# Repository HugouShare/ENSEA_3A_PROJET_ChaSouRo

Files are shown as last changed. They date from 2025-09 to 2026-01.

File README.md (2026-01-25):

# 🤖 ChaSouRo 🤖


  

## 📝 Rapport de projet

Pour consulter notre rapport de projet [cliquez ici](Documents/Rapport%20de%20projet.md)  

---

## 👨🏽 Équipe

<div align="left">

   **🙋‍♂️ [Hugo CARVALHO FONTES](https://github.com/HugouShare)**

   **🙋‍♂️ [Nelven THÉBAULT](https://github.com/NelvTheb)**

   **🙋‍♂️ [Hugo CORDI](https://github.com/Lynxlegrand)**

   **🙋‍♂️ [Arthur Cesar NJITCHOU NKWA](https://github.com/ArthurNjitchou)**

</div>

## ⚙️ Introduction

- Nous réalisons ce projet dans le cadre de notre dernière année d'étude en spécialité électronique et systèmes embarqués à l'[ENSEA](https://www.ensea.fr/fr) située à Cergy.
- Le but du projet est de réaliser deux robots : l'un étant le robot chat et l'autre le robot souris. Les deux robots évoluent ensuite de manière autonome sur une table. Le but du jeu est alors le suivant : le robot chat doit tenter d'attraper le robot souris qui doit donc tenter d'échapper au robot chat. Une fois que le robot chat attrape le robot souris, les rôles s'inversent et la partie continue. 

## 🎯 Missions & Objectifs

Les missions principales sont les suivantes (réparties selon différents niveaux) :
  - **Niveau 0 :**
    - Le robot se déplace
    - Il ne tombe pas de la table
  - **Niveau 1 :**
    - Il détecte et se dirige vers un objet
    - Ou s’en éloigne s’il n’est pas le chat
  - **Niveau 2 :**
    - Il change de comportement (proie/prédateur) après un contact
    - Il fonctionne avec plusieurs robots sur la table
  - **Niveau 3 :**
    - Il n’est pas affecté par les obstacles hors de la table
    - Il est donc capable de se localiser

Dans notre cas à nous, nous choisissons le niveau 1 voire potentiellement, selon notre avancement, le niveau 2.  

## ⌚ Timeline du projet  

```mermaid
%%{init: {"theme":"default", "themeVariables": {
  "primaryColor": "#4F46E5",
  "primaryTextColor": "#ffffff",
  "primaryBorderColor": "#312E81",
  "lineColor": "#6366F1",
  "secondaryColor": "#E0E7FF",
  "tertiaryColor": "#A5B4FC"
}}}%%

timeline
    section Phase 1 - conception du PCB
      Séance 1 : Point réunion + schéma architectural / BOM
      Séance 2 et 3 : Schéma électronique annoté
      Séance 4 : Corrections Schéma / BOM Finale
      Séance 5 : Point réunion + placement
      Séance 6 : Placement corrigé
      Séance 7 et 8 : Routage
      Séance 9 et 10 : Corrections Routage, export...
    section Phase 2 - mécanique 3D + prise en main et programmation des différents capteurs et actionneurs
      Séance 1 : Point réunion + architecture de subsomption + architecture schéma logicielle + soudure composants sur PCBs + vérification du bon fonctionnement des PCBs
      Séance 2 et 3 et 4 : Prise en main & programmation du LiDar + accéléromètre + écran OLED + module bluetooth avec développement application apk
      Séance 5 : Point réunion + vérification du bon fonctionnement des différents modules
      Séance 6 et 7 et 8 : Développement de l'odométrie + programmation des moteurs + 1x TOF puis 4x TOFs + modification de la structure mécanique du robot pour intégration des 4 TOFs et écran OLED
      Séance 9 et 10 : Impression 3D de la structure mécanique du robot + début de l'intégration des différents modules + finalisation de la programmation des 4x TOFs ensemble 
    section Phase 3 - Intégration, tests & vérifications
      Séance 1 et 2 : Point réunion + intégration, tests & vérifications
      Séance 3 : DEMONSTRATION FINALE
```

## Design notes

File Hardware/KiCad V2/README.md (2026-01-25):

# Modifications sur la V1

- Problèmes sur la taille des empreintes pour les capacités >= 10uF -> Passage en 0603
- Changement pad sw wurth vers un connecteur (plus propre) -> JST_PH Batterie +/- (Pin_x2) en JS_PH_ Batterie +/- et +/IN du switch wurth (Pin_x4)
- Erreur sur un des deux drivers où les silkscreen des OUT1 et OUT2 sont inversé par rapport au pin (Quand on se place dans le sens avec TX4/RX4 du ST-Link -> Driver gauche)
- Ajout Silkscreen sur ST-Link pour simplifier la connexion
- Modification schématique/Nom du bon NMOSFET -> SQ2310ES
- Changement de la capacité de découplage du VDDA : 47uF -> 22uF
- Oublie des capacités pour limiter les rebonds sur USER1 et USER2 -> ajout de 0.1uF
- Inversion sur le PCB des RX3/TX3 sur les pins PB10/PB11 du STM32
- Problème d'angle droit sur la ligne SDA3 enlevé (peut-être incidence sur l'I2C3)
---
Modification non faite mais à connaître pour de futurs projets 
- Utilisation du PB4 (BOOT0) pour le xshunt du ToF1 → pose problème car relié en interne à un GPIO relié ici au FWD ou REV d'un driver moteur → réinitialise la carte.
    - Solution : ne jamais utiliser la broche `BOOT0` pour autre chose même si l'on est censé pouvoir le faire

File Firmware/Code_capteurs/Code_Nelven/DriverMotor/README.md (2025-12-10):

# Fonctionnement

## Init 

- Fonction `Init_motors()` qui démarre les PWM et fais tourner le robot sur lui même à gauche puis à droite.

## Principe
- Une structure de pointeurs motorDriver à été mis en place qui associe à un moteur L ou R, son timer et son FWD/REV.
- 2 fonctions
	- `Motors_Set()` qui vient modifier une structure avec les valeurs de vitesses et durées souhaitées dans les deux moteurs
	- `Motor_SetSpeed()` qui applique dans la tâche `Task_motor` dédiée et permet au tout de ne pas être bloquant 

## Utilisation

Ici configuré dans le callback des boutons 2 consignes :  
- une où le robot tourne sur lui même sens droite
- une où le robot avance tout droit lentement

Reste à mettre en plac ue fonction pour corrige la trajectoire qui n'est pas parfaitement droite.

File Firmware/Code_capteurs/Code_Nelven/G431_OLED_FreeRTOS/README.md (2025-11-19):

# ATTENTION

Drivers dans ../Drivers à ajouter dans le path pour que ça marche

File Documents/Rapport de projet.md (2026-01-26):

# Sommaire  

<details>
<summary><strong>📑 Sommaire</strong> (cliquer pour dérouler)</summary>

<br>

- [Contexte général du projet](#contexte-général-du-projet)
- [Aspects techniques liés au projet](#aspects-techniques-liés-au-projet)
  - [Schéma d'architecture fonctionnelle](#schéma-darchitecture-fonctionnelle)
  - [Diagramme des tâches](#diagramme-des-tâches)
  - [Organisation du projet sur STM32CubeIDE](#organisation-du-projet-sur-stm32cubeide)
    - [Description détaillée fichiers sources](#-description-détaillée-fichiers-sources)
    - [Description détaillée fichiers headers](#-description-détaillée-fichiers-headers)
- [Point HARDWARE](#point-hardware)
  - [Composants](#composants)
  - [Schéma électrique](#schéma-électrique)
  - [Routage](#routage)
    - [Positionnement face F/B](#positionnement-face-fb)
    - [Positionnement sur la carte](#positionnement-sur-la-carte)
- [Point FIRMWARE](#point-firmware)
  - [Choix d’architecture logicielle](#choix-darchitecture-logicielle)
  - [Choix de FreeRTOS](#choix-de-freertos)
  - [Gestion de la mémoire](#gestion-de-la-mémoire)
  - [Choix et description des comportements du robot](#choix-et-description-des-comportements-du-robot)
- [Problèmes rencontrés lors du projet](#problèmes-rencontrés-lors-du-projet)
  - [Hardware](#hardware)
  - [Firmware](#firmware)
- [Rapport individuel des tâches réalisées](#rapport-individuel-des-tâches-réalisées-au-sein-du-projet)
- [Résultat final le jour J](#résultat-final-le-jour-j)
- [Conclusion du projet](#conclusion-du-projet)

</details>  

# Contexte général du projet  

Comme expliqué précédemment, le but de notre projet est de concevoir un robot capable de jouer au jeu du chat et de la souris de manière complètement autonome sur une table.   
Pour plus d'informations sur le projet : [cliquez ici](Descriptif%20du%20projet.pdf)  

Pour se faire, seuls les composants utilisés dans le projet nous sont imposés : [liste des composants](Liste%20des%20composants%20disponibles.pdf)  

Charge à nous :  
- de développer une PCB
- de programmer les différents modules : capteurs, actionneurs, écran OLED et module de communication bluetooth
- d'intégrer tous les modules ensemble, de tester et vérifier le bon fonctionnement de l'ensemble

# Aspects techniques liés au projet

## Schéma d'architecture fonctionnelle  

Après une première réunion portant sur l'architecture fonctionnelle de notre robot, voici le schéma fonctionnel que nous adoptons pour notre robot :  
  

## Diagramme des tâches  

Voici un diagramme des tâches qui résume le fonctionnement de notre robot :

  

Les priorités étant définies dans le fichier de configuration `freeRTOS_tasks_prority.h` :

```c
#define ADXL_TaskRead_PRIORITY 2
#define ADXL_TaskPrint_PRIORITY 1

#define task_ROOMBA_PRIORITY 6
#define task_CHAT_PRIORITY 2
#define task_SOURIS_PRIORITY 2
#define task_EDGE_PRIORITY 6

#define task_Control_PRIORITY 5

#define task_ENC_D_Update_PRIORITY 6
#define task_ENC_G_Update_PRIORITY 6
#define task_Odom_Update_PRIORITY 3

#define task_BLUETOOTH_TX 1
#define task_BLUETOOTH_RX 2

#define task_LIDAR_Update_PRIORITY 3

#define task_motor_PRIORITY 5

#define task_screen_PRIORITY 1
```

## Organisation du projet sur STM32CubeIDE  

D'un point de vue global, nous avons choisi d'organiser notre projet de la manière suivante :  

| Fichiers sources | Fichiers headers |
|---|---|
|  |  |  

### 📝 Description détaillée fichiers sources

#### 📦 Dossier `actuators/` – Gestion des actionneurs

| Fichier | Rôle |
|---|---|
| **behavior.c** | Implémente les comportements de haut niveau (navigation et stratégie de déplacement). |
| **control.c** | Contient les fonctions de contrôle moteur, coordination PID, gestion des vitesses/couple. |
| **encoder.c** | Gestion des encodeurs : lecture des ticks, calcul de vitesse et position. |
| **motor.c** | Interface bas niveau pour piloter les moteurs (PWM, direction, enable/disable). |
| **pid.c** | Implémentation des régulateurs PID utilisés par `control.c` et `behavior.c`. |

#### 📦 Dossier `bluetooth/` – Communication Bluetooth

| Fichier | Rôle |
|---|---|
| **bluetooth.c** | Gestion du module Bluetooth : initialisation, envoi/réception de données. |

#### 📦 Dossier `oled_screen/` – Afficheur OLED

| Fichier | Rôle |
|---|---|
| **oled.c** | Gestion d’un écran OLED : affichage de texte, images, et initialisation. |

> Remarque : Drivers OLED importé depuis internet et modifié se situant dans le dosser `Drivers/OLED/`.

#### 📦 Dossier `sensors/` – Capteurs du robot

| Fichier | Rôle |
|---|---|
| **accelerometers.c** | Lecture de l’accéléromètre (IMU), calibration, filtrage. |
| **lidar.c** | Interface avec un LiDAR : récupération des distances, gestion du capteur. |
| **tofs.c** | Gestion des capteurs Time-of-Flight. |

#### 🧵 FreeRTOS

| Fichier | Rôle |
|---|---|
| **app_freertos.c** | Définition des tâches FreeRTOS, files de messages, mutex et scheduling. |

#### ⚙️ Core système

| Fichier | Rôle |
|---|---|
| **main.c** | Point d’entrée du programme, initialisations des différents capteurs, créations des différentes tâches et démarrage du RTOS. |
| **syscalls.c** | Implémente les fonctions système nécessaires (malloc, printf…). |
| **sysem.c** | Gestion du système et interrupt handlers (auto-généré). |
| **system_stm32g4xx.c** | Configuration de l’horloge système et initialisation MCU. |

#### 🔧 Drivers Hardware Abstraction Layer (HAL)

| Fichier | Rôle |
|---|---|
| **dma.c** | Initialisation du DMA pour les transferts mémoire ↔ périphériques. |
| **gpio.c** | Configuration des broches GPIO (mode, pull-up/down, vitesse…). |
| **i2c.c** | Initialisation du bus I2C utilisé par IMU, OLED, ToF. |
| **tim.c** | Configuration des timers : PWM moteurs, interruptions, timebase. |
| **usart.c** | Gestion de la communication série UART (console, Bluetooth). |
| **stm32g4xx_hal_msp.c** | Fonctions MSP auto-générées : clocks, GPIO, interruptions. |
| **stm32g4xx_it.c** | Gestion des interruptions globales du microcontrôleur. |
| **stm32g4xx_hal_timebase_tim.c** | Gestion de la base de temps HAL via TIM. |  

### 📝 Description détaillée fichiers headers

#### 📦 Dossier `oled_screen/` – Gestion de l’OLED

| Fichier | Rôle |
|---|---|
| **bitmaps.h** | Ressources graphiques (icônes, images) utilisées par l’écran OLED. |  

#### 🧵 FreeRTOS

| Fichier | Rôle |
|---|---|
| **FreeRTOSConfig.h** | Configuration du kernel FreeRTOS (priorités, timers, heap…). |
| **freeRTOS_tasks_priority.h** | Définition des priorités de tâche et organisation du multitâche. |

#### ⚙️ Core du programme

| Fichier | Rôle |
|---|---|
| **main.h** | Déclarations globales, includes principaux et prototypes de `main.c`. |

# Point HARDWARE  

> Remarque :  
> Pour évaluer la partie hardware, merci de vous référer au KiCAD V2, étant donné que les problèmes identifiés ont été corrigés et le schéma refait au propre. La V1 n’a pas été modifiée afin de rester la plus fidèle possible à la version physique reçue et utilisée.

### Composants

Nous avions pour les missions principales, une liste de composants que nous devions utiliser ce qui a conditionné nos choix mais les a aussi simplifiés.
Voici les composants ajoutés :
- Écran OLED → ssd1306 
  - écran personnel de Nelven pour pouvoir le comprendre et le réutiliser pour de prochains projets.
- Bipper
  - Ajout d'un bipper pour avoir un différent moyen des autres groupes de notifier des choses (mode chat par exemple).
- Connecteurs JST-PH
  - Un pas de 2.0mm permettant de mettre tous les connecteurs sur une face du PCB ce que ne permettait pas les JST-XH (2.54mm) et en étant plus simple à souder/connecter que des JST-SH(1.0mm).

### Schéma électrique

Dans cette partie il n'y a pas grand chose à ajouter, étant donné que les circuits on été réalisé à l'aide des datasheet, de mes propres connaissances sur d'anciens projets.

### Routage

#### Positionnement face F/B

Un choix a été effectué afin de simplifier la soudure :

- Tous les composants passifs, régulateurs et transistors sont placés sur une même face du PCB.
- Tous les connecteurs, SoC, quartz, condensateurs électrolytiques, LED et boutons sont placés sur l’autre face.

De cette manière, sur la face inférieure, il est possible d’observer les circuits et de souder l’ensemble des petits composants au four en une seule opération.
Sur la face supérieure (visible) se trouvent les SoC, les connecteurs et les LED, c’est-à-dire les unités et modules nécessaires au fonctionnement du système, ainsi que les composants les plus volumineux à souder.

#### Positionnement sur la carte

J'ai choisi de ne pas mélanger les parties puissance et signal à différents endroits de la carte. En considérant que le bas du PCB se trouve au niveau du branchement de la batterie, j'ai positionné les composants de la manière suivante :

- **Bas du PCB → partie puissance**
  - Arrivée de la batterie [bas gauche]  
  - Interrupteur d’alimentation ON/OFF [bas gauche]  
  - Convertisseurs $V_{BATT}/5V$ et $5V/3.3V$ [bas milieu]  
  - Condensateur électrolytique [bas milieu]  
  - Drivers moteurs (alimentés en $V_{BATT}$)  
    - Carte retournée sur le robot : driver droit à [bas gauche] et driver gauche à [bas droit], pour simplifier les branchements  

- **Milieu/Haut du PCB → partie signal**
  - MCU [milieu]  
  - Connecteur ST-Link [haut droit]  
  - ADXL [haut droit]  
  - Quartz [milieu] avec ses deux condensateurs de l’ordre de la dizaine de nanofarads  
  - Boutons [haut gauche]  
  - 3 LED [haut gauche]  
    - **ROUGE** : $3.3V$, allumée en permanence lorsque la carte est sous tension  
    - **BLEU** : LED1 pour programmation/debug  
    - **VERT** : LED2 pour programmation/debug

À noter que j'ai respecté les consignes de routage pour le `convertisseur buck` fournies dans la datasheet, ce qui occupe une certaine place sur la carte.

Et tout autour de la carte les différents connecteurs pour tout relié à la carte.

`Face avant` :

Face avant PCB  

`Face arrière` :

Face arrière PCB  

# Point FIRMWARE  

La partie firmware du projet a été conçue afin de garantir un fonctionnement **modulaire, robuste et évolutif** du robot, tout en respectant les contraintes d’un système embarqué temps réel (ressources mémoire limitées, concurrence des tâches et réactivité élevée).

### Choix d’architecture logicielle  

#### Organisation du code et séparation des modules  

Le code C a été structuré par **fonctionnalité**, chaque module correspondant à un sous-système clairement identifié du robot (capteurs, actionneurs, communication, affichage, comportements). Cette organisation permet :
- une **lisibilité accrue** du code,
- une **maintenance facilitée**,
- une **intégration progressive** et maîtrisée des différents modules.

Chaque dossier (par exemple `sensors/`, `actuators/`, `bluetooth/`, `oled_screen/`) contient les fichiers sources associés à un module donné, incluant les structures de données, les fonctions de configuration et la logique de traitement.

#### Convention d’intégration des modules (init, tâches et callbacks)  

Afin de faciliter l’intégration et d’assurer une architecture cohérente sur l’ensemble du projet, une **convention commune** a été adoptée pour tous les drivers.

Pour chaque module :
- une fonction **`XXX_init()`** est définie afin d’initialiser le périphérique (configuration matérielle, paramètres internes, états initiaux),
- une fonction **`XXX_task_create()`** est fournie pour créer la ou les tâches FreeRTOS associées au module.

Ces deux fonctions sont **appelées explicitement dans `main.c`**, ce qui permet :
- de centraliser l’initialisation du système,
- de maîtriser précisément l’ordre de démarrage des modules,
- de simplifier l’ajout ou le retrait d’un module sans impacter les autres parties du code.

Lorsque l’utilisation de **callbacks** est nécessaire (interruptions, réception UART, DMA, timers…), ceux-ci sont **redéfinis uniquement dans `main.c`**. Les callbacks HAL appellent ensuite des fonctions dédiées du type **`XXX_callback()`** appartenant au module concerné.

Cette approche permet :
- d’éviter toute **double redéfinition de callbacks**, source potentielle de conflits,
- de conserver une **séparation claire** entre la couche HAL et la logique applicative,
- d’améliorer la lisibilité et la maintenabilité du code.

#### Utilisation de drivers dédiés  

Le choix de développer des **drivers spécifiques** pour chaque périphérique (LIDAR, TOF, ADXL, moteurs, encodeurs, Bluetooth…) permet d’abstraire les accès bas niveau (I2C, UART, GPIO, timers) et de proposer une interface logicielle homogène.

Les drivers s’appuient sur la HAL STM32 pour les accès matériels, tout en encapsulant la logique propre à chaque capteur ou actionneur. Cette approche améliore :
- la **réutilisabilité** du code,
- la **robustesse de l’intégration**,
- la facilité de test et de débogage.

### Choix de FreeRTOS  

L’utilisation de **FreeRTOS** s’est imposée au vu de la complexité du système et du nombre de traitements à effectuer en parallèle : lecture capteurs, contrôle moteur, communication Bluetooth et prise de décision.

Chaque fonctionnalité critique du robot est implémentée sous forme de **tâche FreeRTOS dédiée**, permettant :
- une **exécution concurrente maîtrisée**,
- une **priorisation fine** des traitements,
- une meilleure **réactivité temps réel**.

Les **priorités des tâches FreeRTOS sont toutes définies dans un header dédié** (`freeRTOS_tasks_priority.h`), ce qui permet :
- une vision globale et centralisée de l’ordonnancement,
- une modification simple des priorités sans impacter le reste du code,
- une meilleure cohérence entre les différents modules.

La synchronisation entre tâches est assurée via les mécanismes FreeRTOS classiques (sémaphores, mutex, notifications), garantissant la cohérence des données partagées.

### Gestion de la mémoire  

Les contraintes mémoire, en particulier sur la RAM, ont fortement influencé les choix firmware. L’utilisation de FreeRTOS et de certains modules gourmands (LIDAR, OLED) a conduit à :
- une gestion stricte des piles de tâches,
- une limitation des buffers statiques,
- le retrait de l’écran OLED dans la version finale afin d’éviter tout stack overflow.

Le tas FreeRTOS a été dimensionné à sa valeur maximale acceptable (~25 kB) pour garantir la stabilité du système.

### Choix et description des comportements du robot  

Le comportement global du robot repose sur une **machine à états finis** comportant quatre modes principaux : ROOMBA, CHAT, SOURIS et EDGE. Chaque mode correspond à un objectif précis et exploite les données issues des capteurs.

#### Mode ROOMBA  

Le mode ROOMBA correspond à un comportement d’exploration autonome :
- déplacement continu,
- évitement des bords via les capteurs TOF et le LIDAR,
- changements de direction pseudo-aléatoires.

Il constitue le **mode par défaut** lorsque aucune cible n’est détectée.

#### Mode CHAT  

Le mode CHAT est activé lorsqu’une cible est détectée :
- traitement des données LIDAR (tri, clustering, sélection de la cible),
- poursuite active de l’adversaire,
- ajustement dynamique de la trajectoire par asservissement moteur.

#### Mode SOURIS  

Le mode SOURIS correspond à un comportement de fuite :
- activation lorsque le robot est détecté ou poursuivi,
- recherche d’un espace libre,
- déplacements rapides tout en évitant les bords.

#### Mode EDGE  

Le mode EDGE est un mode de sécurité prioritaire :
- déclenché dès qu’un bord est détecté,
- arrêt ou recul immédiat du robot,
- réorientation avant reprise d’un autre mode.

Ce mode est volontairement prioritaire afin de garantir la sécurité du robot, indépendamment du comportement en cours.

### Coordination des comportements  

Les transitions entre les différents modes sont déclenchées par les données capteurs, le contexte global du robot et les événements temps réel. Cette organisation permet d’obtenir un comportement **autonome, cohérent et réactif**, tout en restant facilement extensible.

# Problèmes rencontrés lors du projet    

### Hardware

Du côté Hardware, les problèmes rencontrés ont été solutionnés dans la V2 que l'on trouve dans `Hardware/KiCad V2/` avec readme associé qui explique les changement :

> Remarque : la carte physique utilisée reste la V1 ; cette V2 constituerait donc sa remplaçante dans le cas où l’on souhaiterait améliorer le projet.

#### Modifications sur la V1

- Problèmes sur la taille des empreintes pour les capacités >= 10uF -> Passage en 0603
- Changement pad sw wurth vers un connecteur (plus propre) -> JST_PH Batterie +/- (Pin_x2) en JS_PH_ Batterie +/- et +/IN du switch wurth (Pin_x4)
- Erreur sur un des deux drivers où les silkscreen des OUT1 et OUT2 sont inversé par rapport au pin (Quand on se place dans le sens avec TX4/RX4 du ST-Link -> Driver gauche)
- Ajout Silkscreen sur ST-Link pour simplifier la connexion
- Modification schématique/Nom du bon NMOSFET -> SQ2310ES
- Changement de la capacité de découplage du VDDA : 47uF -> 22uF
- Oublie des capacités pour limiter les rebonds sur USER1 et USER2 -> ajout de 0.1uF
- Inversion sur le PCB des RX3/TX3 sur les pins PB10/PB11 du STM32
- Problème d'angle droit sur la ligne SDA3 enlevé (peut-être incidence sur l'I2C3)
---
> [!IMPORTANT]
> Modification non faite mais à connaître pour de futurs projets 
> - Utilisation du PB4 (BOOT0) pour le xshunt du ToF1 → pose problème car relié en interne à un GPIO relié ici au FWD ou REV d'un driver moteur → réinitialise la carte.
>    - Solution : ne jamais utiliser la broche `BOOT0` pour autre chose même si l'on est censé pouvoir le faire

#### PIN BOOT0

Même si cela constitue une répétition par rapport aux lignes précédentes, nous tenons à insister sur le fait que, sur les STM32, bien qu’il soit parfois possible d’utiliser la broche `BOOT0` selon le microcontrôleur, il est fortement déconseillé de le faire. En effet, cela peut entraîner des problèmes de fonctionnement, comme observé avec les capteurs ToF ci-dessus, mais également compliquer la programmation.

Dans notre cas, nous avons dû utiliser `STM32CubeProgrammer` afin de configurer par logiciel la mémoire de démarrage (boot memory). Ainsi, au redémarrage, la carte démarrait correctement sur le programme flashé, alors qu’auparavant il était nécessaire de laisser la carte constamment sous tension si l’on voulait éviter de devoir reprogrammer le code avec un ST-Link.

### Firmware

Du côté firmware, l’un des premiers problèmes que nous avons dû résoudre est la gestion de la mémoire, et plus particulièrement de la RAM (~91 %), étant donné que notre ROM n’a atteint que ~41 %. Nous avons donc fait le choix de retirer l’écran OLED dans la version finale afin d’éviter tout stack overflow et de monter le tas FreeRTOS à sa valeur maximale avant overflow (25 000 octets, soit environ 25 kB).

Deux autres problèmes majeurs ont été rencontrés durant le projet. D’une part, le LIDAR présentait des angles morts, ce qui a nécessité une adaptation de la stratégie de gestion des trames envoyées par le capteur, ainsi qu’un ajustement de la fréquence de traitement du buffer stockant les données issues de ces trames, afin d’améliorer la couverture et la fiabilité de la détection. D’autre part, le réglage des correcteurs PID s’est avéré particulièrement délicat, demandant de nombreuses itérations et de longues phases de tests expérimentaux pour obtenir un comportement stable et satisfaisant du robot.

# Rapport individuel des tâches réalisées au sein du projet  

Suite à cela, après une nouvelle réunion, chaque membre du groupe se voit attribuer diverses missions.  
Voici un récapitulatif de ce que chaque membre du groupe aura réalisé au sein du projet...  

### Nelven THEBAULT  

`Hardware` :
- PCB
  - Conception du PCB finalement retenu
  - Schéma électrique
  - Routage
  - Soudure
  > J’explique mes choix par rapport au cahier des charges et à nos réunions de projet avec l’équipe dans la partie [Point HARDWARE](#point-hardware).

`Firmware` :
- Module Moteur
  - Conception du **driver moteur** et **task_motor**
  - Conception du code **encodeur (ENC)** ensuite repris par Hugo  pour FreeRTOS
- Module OLED 
  - Conception du **oled.c** et **task_oled** utilisant un driver générique
- Module Bipper
  - Intégration du **Bipper** dans certaines parties du code (mode chat par exemple)
- Intégration des différents modules 

`Mécanique` :
- Participation aux choix pour la conception mécanique avec Arthur
- Impressions 3D de certaines parties
- Assemblage de certaines parties

### Hugo CARVALHO FONTES  

`Hardware` : 
- Conception d'une PCB : schematique & routage
- Soudure des composants sur la carte finale
- Analyses oscilloscope & modification du pin XSHUT1 car disfonctionnnement  

`Software` : 
- Module bluetooth HC-05
  - Création d'une application apk sous android studio afin de pouvoir lancer le robot ou l'arrêter d'urgence, mais aussi afin de recevoir et afficher en temps-réel les coordonnés du robot sur la table

`Firmware` : 
- Module bluetooth HC-05
  - Implémentation du code C en Free-RTOS et avec driver sur STM32G431CBU6
- Module TOFs VL53L0X
  - Implémentation du code C en Free-RTOS et avec driver sur STM32G431CBU6 afin de faire fonctionner 4 TOFs ensemble
- Module accéléromètre ADXL345
  - Implémentation du code C en Free-RTOS et avec driver sur STM32G431CBU6
- Intégration & vérification de tous les différents modules afin d'obtenir un robot fonctionnel  

### Arthur César NKWA NJITCHOU  

`Hardware` :
- Conception d'un PCB : Réalisation de la schématique et du routage du circuit imprimé (PCB)
- Recherche de composants : Participation active à la sélection des composants électroniques
- Soudure : Assemblage et soudure des composants sur le PCB final avec l'équipe

`Software` :
- Développement en C : Implementation du code pour l'accéléromètre ADXL345, permettant de détecter les chocs brusques lors des collisions du robot

`Mécanique` :
- Conception des supports : Création de supports pour les capteurs TOF et l'écran, ainsi que perçage pour l'interrupteur et le buzzer
- Amélioration des pattes : Optimisation des pattes des bases supérieures pour une meilleure stabilité
- Impression 3D : Impression des différentes parties du robot à l'aide d'une imprimante 3D
- Assemblage partie mécanique du robot.

### Hugo CORDI  

`Software/Firmware` :
- Module LIDAR
  - Développement du traitement des données LIDAR pour la détection des ennemis
  - Implémentation d’algorithmes de clustering, tri et sélection de la cible
  - Exploitation des données pour alimenter les décisions de poursuite et de fuite du robot
  - Implémentation en C embarqué sous FreeRTOS sur STM32, avec gestion des tâches, de la mémoire et synchronisation via sémaphores, notifications et mutex
  - Intégration du module LIDAR avec les autres capteurs et les comportements globaux du robot

- Module encodeurs roues
  - Gestion des encodeurs incrémentaux pour l’estimation du déplacement du robot
  - Implémentation d’un asservissement en position à l’aide de correcteurs PID
  - Réglage et validation des performances de déplacement
  - Implémentation en C embarqué sous FreeRTOS sur STM32, avec communication et synchronisation avec les autres modules du système
  - Contribution à l’intégration globale du robot afin d’obtenir un système autonome et fonctionnel

- Code de comportement du robot
  - Conception et implémentation d’une machine à états à quatre modes (ROOMBA, Chat, Souris, Edge)
  - Gestion des transitions d’états en fonction des données capteurs et du contexte
  - Implémentation en C embarqué sous FreeRTOS, avec coordination des tâches et synchronisation entre modules pour assurer un comportement autonome et réactif  

# Résultat final le jour J  

`Robot`:

Robot  

`Test détection de bord en mode ROOMBA` :

https://github.com/user-attachments/assets/2c88ca6d-3d82-48a8-8c14-df83039007b4

cf. chemin : <Images et videos pour rapport de projet/Test detection de bord mode ROOMBA.mp4>  

`Test plusieurs robots qui sont chats` :  

https://github.com/user-attachments/assets/9dab9074-2687-4d48-a438-ce1f9aacd102

cf. chemin : <Images et videos pour rapport de projet/Test plusieurs chats.mp4>  

# Conclusion du projet   

Le projet a permis de concevoir un robot autonome capable de jouer au jeu du chat et de la souris, en intégrant de manière cohérente la partie hardware, firmware et mécanique. Nous avons pu appliquer nos connaissances en conception de PCB, programmation C et utilisation de FreeRTOS, tout en respectant les contraintes des composants imposés.

Les différentes étapes, de la conception des schémas et du routage à l’implémentation des modules moteurs, capteurs et communication, ont permis de créer un robot fonctionnel et robuste. Ce projet nous a également confrontés à des problématiques concrètes, telles que la gestion de la mémoire, les choix de routage pour éviter les interférences et la configuration des broches critiques comme BOOT0. Il a renforcé notre capacité à travailler en équipe, à coordonner les tâches entre hardware, firmware et mécanique, et à documenter nos choix pour faciliter la maintenance et l’évolution future du robot.

Enfin, nous sommes fiers d’avoir atteint notre objectif : le robot détecte les bords et peut jouer au chat et à la souris, malgré certaines limitations comme l’écran, la vitesse, l'ajout de la tâche qui permet le  changement de rôle lors d'un choc, du déplacement à optimiser et la détection à calibrer plus finement. Ce succès constitue une expérience complète et enrichissante dans le domaine des systèmes embarqués.

<p float="left">

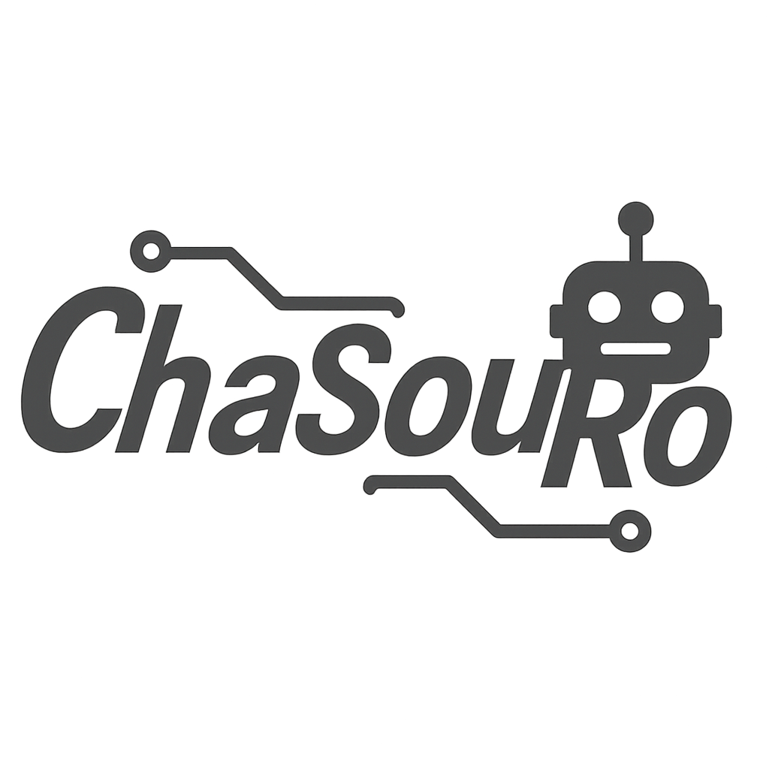
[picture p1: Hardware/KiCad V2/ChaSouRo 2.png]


</p>

`Photo de l'équipe ChaSouRo` :

Equipe projet

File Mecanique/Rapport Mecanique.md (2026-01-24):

# Partie Mécanique du Projet Chat et Souris

Nous nous sommes inspirés de la version de base fournie par le professeur [ici](https://cad.onshape.com/documents/7eabf90e47e8c8553dc09658/w/3dcd7f2858a0589a4cbae030/e/145e161f6c9d99158433c942).

## Modifications et Améliorations

### Conception des Supports
- **Supports TOF** : Création de supports robustes pour les capteurs TOF, optimisant l'alignement pour une détection précise des obstacles.



- **Support de l'Écran** : Développement d'un support ergonomique pour l'écran, garantissant une visualisation claire tout en préservant la compacité du robot.



### Perçage et Assemblage
- **Perçage** : Réalisation de trous pour intégrer l'interrupteur et le buzzer, assurant une installation harmonieuse des composants électroniques.
- **Optimisation des Pattes** : Amélioration des pattes de la base supérieure pour renforcer la stabilité et l'équilibre du robot lors de ses déplacements. Nous avons effectué des tests pour obtenir les dimensions exactes, garantissant ainsi que chaque composant s'encastre facilement et puisse être retiré sans résistance excessive.

WhatsApp Image 2026-01-24 at 09 39 03

**Base supérieure : 1. trous buzzer, 2. trous interrupteur 3. Pattes**

### Impression 3D
- **Fabrication** : Impression 3D de diverses pièces du robot, permettant un ajustement précis au design global et facilitant la personnalisation des composants.

## Assemblage
Assemblage de tous les composants afin de permettre les tests logiciels.



**Assemblage final**

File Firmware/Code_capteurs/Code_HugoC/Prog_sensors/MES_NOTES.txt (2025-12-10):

##### CONFIGURATION #####
0-Mettre les inits dans le main.c et les includes dans main.h
1-Ouvrir STM32CubeProgrammer et configurer les Option Bytes du microcontroller (Voir dossier concerné)
2-Remplacer dans les headers "stm32l4xx_hal.h" par "stm32g4xx_hal.h"
3-Dans l'ioc, activer le DMA pour l'usart approprié
4-Dans l'ioc, activer PWM generation pour le gpio de controle de la vitesse du LIDAR
5-Dans l'ioc, activer les Hooks (pour les stack overflow et les malloc) et highwatermark pour l'espace mémoire
6-Flash le code de la carte

##### MES NOTES #####

- finir le code de détection des ennemis
- régler les encodeurs
- faire les task et la machine à états
- faire le code de l'odométrie
- tout mettre sous RTOS
- intégrer le code dans le vrai capteur

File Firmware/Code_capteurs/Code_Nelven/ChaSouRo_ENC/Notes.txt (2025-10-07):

Explications :
- Encodeur -> TIM4 encoder mode (CH1&CH2) en mode TI1&TI2
- Timer périodique pour lire -> TIM2 (ici à 5 Hz)
- Affichage UART2 à la période de TIM2 de Position 
et vitesse ang avec le nb de tour avant/arrières
grâce à FWD/REV.
- LED2 de la nucleo est toggled dès que le moteur tourne

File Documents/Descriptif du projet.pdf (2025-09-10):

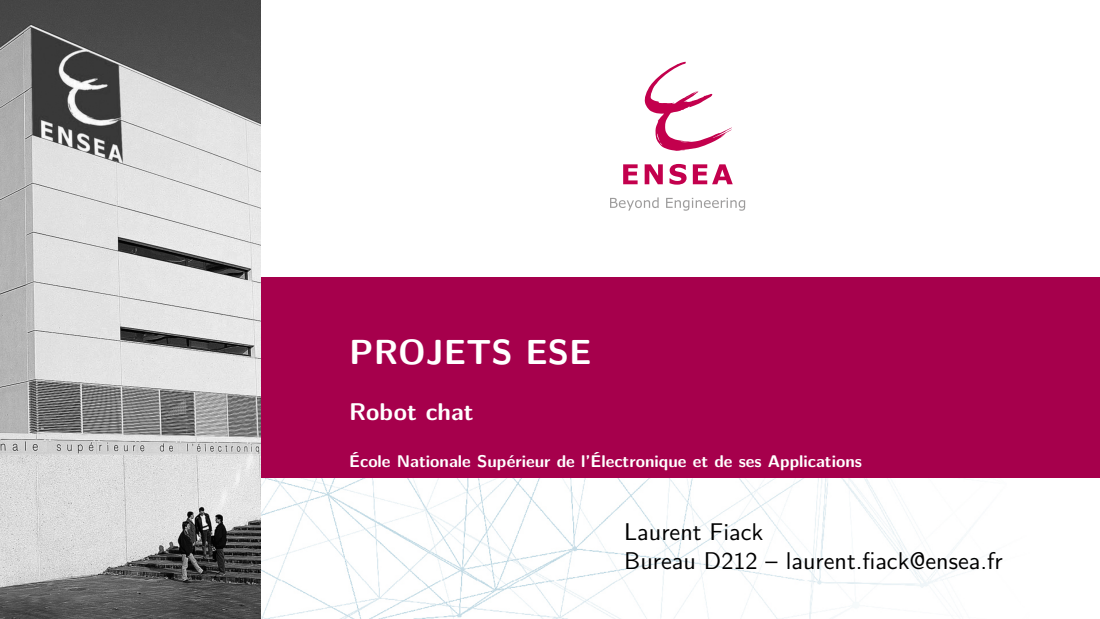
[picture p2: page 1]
PROJETS ESE; Robot chat

École Nationale Supérieur de l’Électronique et de ses Applications

Laurent Fiack
Bureau D212 – laurent.fiack@ensea.fr

Objectifs

## Objectifs

Concevoir un système embarqué de A à Z (du PCB jusqu’au Firmware) Électronique, microcontrôleur, capteurs (conditionnement), actionneurs (drivers), HMI Firmware, drivers, temps-réel
Code de haut niveau, stratégie, comportement...
Projet réparti sur plusieurs modules
Système à Microcontrôleurs → PCB
Noyaux temps-réel → Écriture des drivers logiciels
Initiation à la robotique → Comportement/Stratégie
Projets prétexte pour étudier différents aspects des systèmes embarqués Concevoir un robot mobile qui joue à "chat" avec d’autres robots.
L. Fiack 2 / 10

Projet challenge robot-chat

## Projet challenge robot-chat

Plusieurs robots évoluent sur une table
La table n’a pas de bordure : les robots peuvent tomber Un robot est le "chat"
Il doit attraper un autre robot
Le robot attrapé devient le nouveau "chat"
Et ainsi de suite
L. Fiack 3 / 10

Projet challenge robot-chat

## Sous-objectifs : Robot chat

Projet modulaire.
Objectif simple pour inclure tout le monde. Niveau 0 :
Le robot se déplace,
Il ne tombe pas de la table.
Niveau 1 :
Il détecte et se dirige vers un objet,
Ou s’en éloigne s’il n’est pas le chat.
Niveau 2 :
Il change de comportement (proie/prédateur) après un contact, Il fonctionne avec plusieurs robots sur la table.
Niveau 3 :
Il n’est pas affecté par les obstacles hors de la table,
Il est donc capable de se localiser.
L. Fiack 4 / 10

Projet challenge robot-chat

## Challenge et sous-objectifs

Soyez clair sur vos objectifs !
Pour aller plus loin : Objectifs secondaires, quêtes annexes et challenges Recharge de batterie (avec un câble)
Station de recharge
Robot qui consomme le moins
Robot qui coûte le moins cher
Robot le plus rapide
Fusion de données (IMU, odométrie...) ...
L. Fiack 5 / 10

Déroulement

## Déroulement

Jusqu’à la toussaint
Électronique et mécanique
TP de Microcontrôleurs
Vacances toussaint : Samedi 25 octobre au Dimanche 2 novembre Entre la toussaint et noel
Bibliothèques logicielles
Drivers
Organisation du code
TP de Noyaux temps-réel
Stratégie et comportements
TP d’Introduction à la robotique
Vacances noel : Samedi 20 décembre au Dimanche 4 janvier Après noel
Dernière séance : stratégie et comportements
TP d’Introduction à la robotique
Challenge le vendredi 16 janvier
Fin du semestre : Samedi 17 janvier
Début des PFE : Lundi 19 janvier
L. Fiack 6 / 10

## Attention

Découper le projet
Faire un planning !
Deux semaines de délai (ou plus !) pour les commandes Prendre en compte le temps de soudure, assemblage, tests Commandes au plus tard mi-octobre (ça arrive vite !)
L. Fiack 7 / 10

## Deadlines

10 séances de Systèmes à microprocesseurs
1 | Séance 1 : Schéma architectural / BOM
2 | Séance 2 et 3 : Schéma électronique annoté
3 | Séance 4 : Corrections Schéma / BOM Finale
4 | Séance 5 : Placement
5 | Séance 6 : Placement corrigé
6 | Séance 7 et 8 : Routage
7 | Séance 9 et 10 : Corrections Routage, export...
+ 4h de TD dédié
L. Fiack 8 / 10

## Évaluation

Systèmes à microcontrôleurs : Évaluation des rendus + 1 rapport technique À la toussaint
4 crédits sur 5 dans le module
Noyau temps-réel : Revue de code (git) + 1 rapport + soutenance avant noel

Dernière séance de Noyau Temps-réel
4 crédits sur 5 dans le module
Introduction à la robotique : Démo + Challenges en fin de semestre Dernière séance d’Introduction à la robotique
1 crédit sur 5 dans le module Systèmes électroniques avancés (C’est le même module que Linux Embarqué !)
L. Fiack 9 / 10

## Mécanique

https://cad.onshape.com/documents/7eabf90e47e8c8553dc09658/w/3dcd7f2858a0589a4cbae030/e/145e161f6c9d99158433c942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

Vous pouvez la modifier, ou la reprendre à 0
Deux contraintes à respecter :
Diamètre 170mm (Si c’est un peu différent c’est pas grave) Base du lidar à 90mm du sol, à respecter absolument !
L. Fiack 10 / 10

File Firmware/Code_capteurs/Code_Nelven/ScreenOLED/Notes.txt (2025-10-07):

Pour la prochaine fois :
- Regarder comment faire pour que lorsqu'on descend
ça affiche la suite car pas assez de place sur l'écran
FAIT

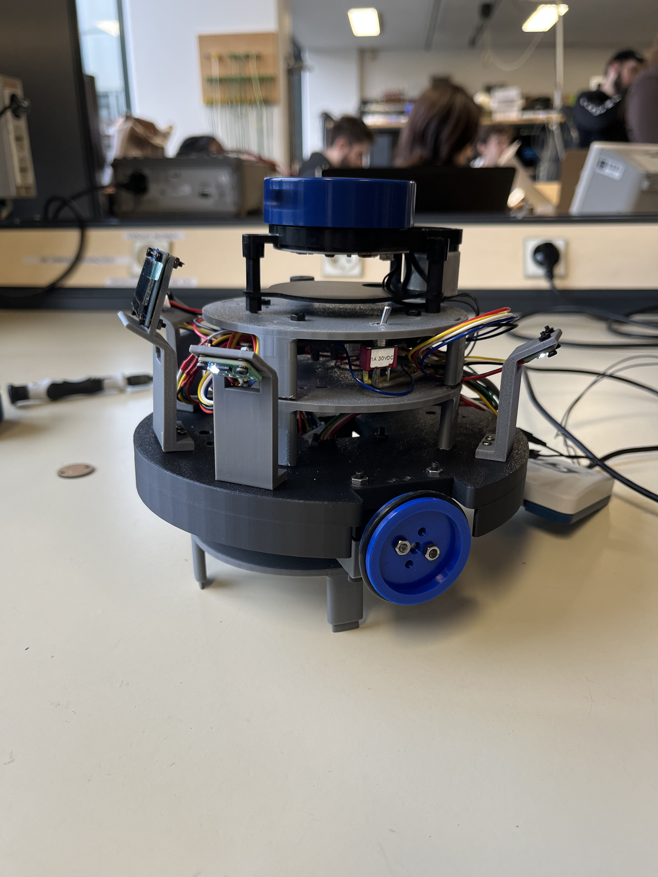
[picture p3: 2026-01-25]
Documents/Images & videos pour rapport de projet/Robot.jpeg

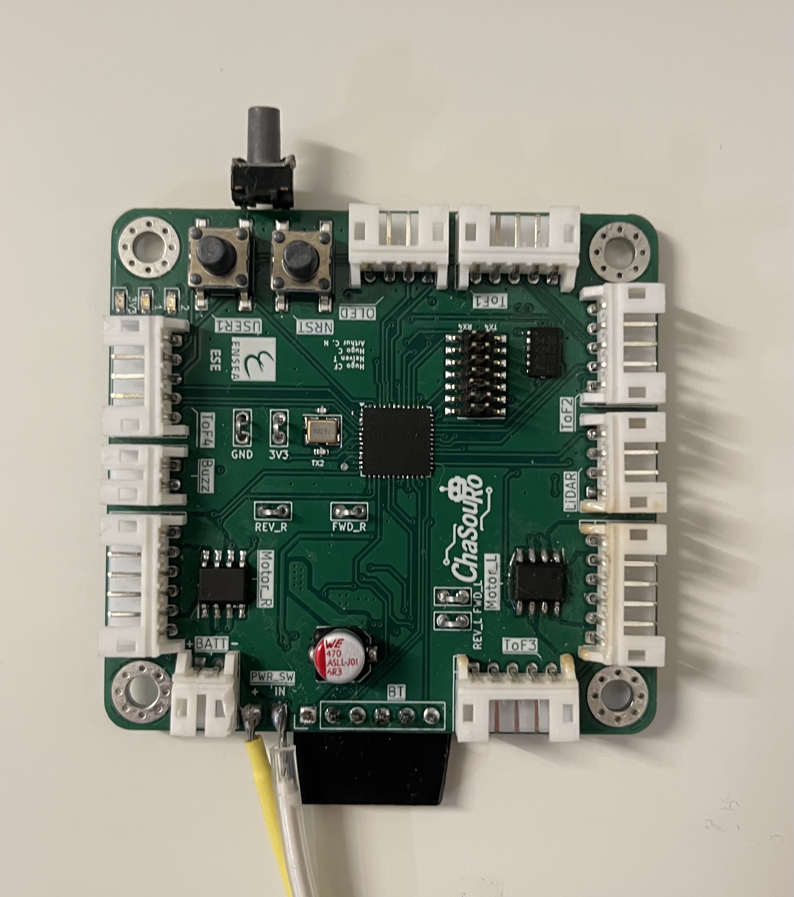
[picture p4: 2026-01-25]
Documents/Images & videos pour rapport de projet/Face avant PCB.jpeg

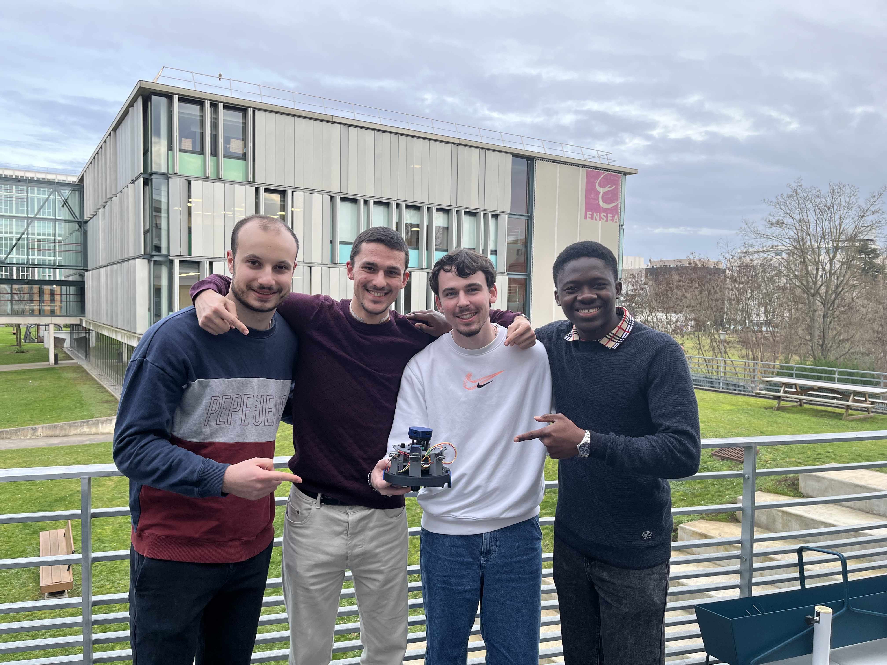
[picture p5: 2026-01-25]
Documents/Images & videos pour rapport de projet/Equipe projet.jpeg

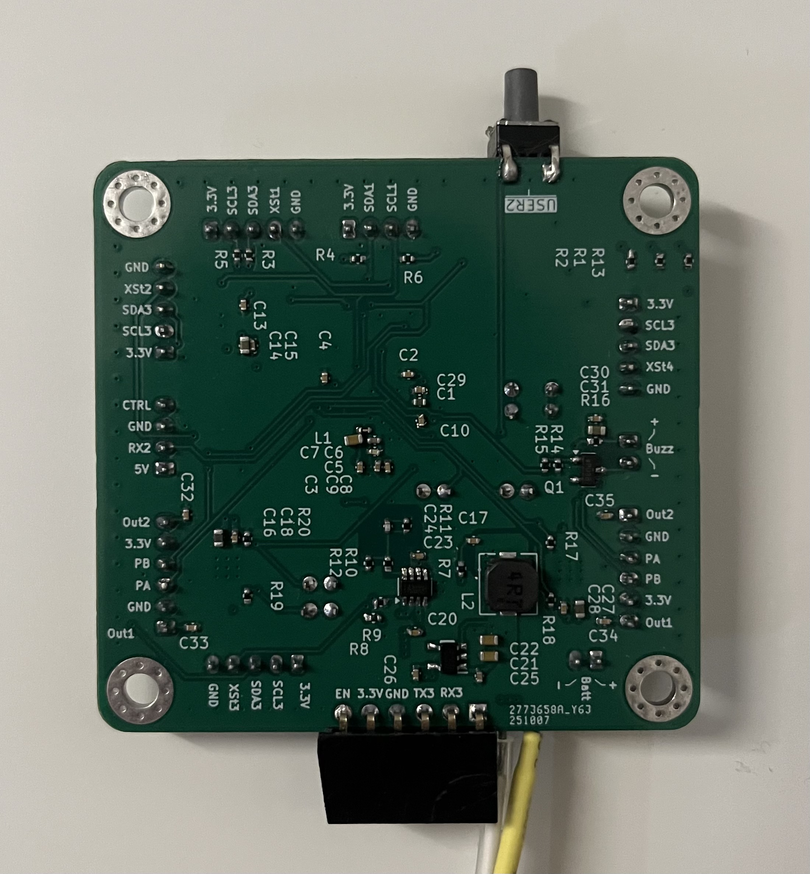
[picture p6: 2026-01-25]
Documents/Images & videos pour rapport de projet/Face arrière PCB.jpeg

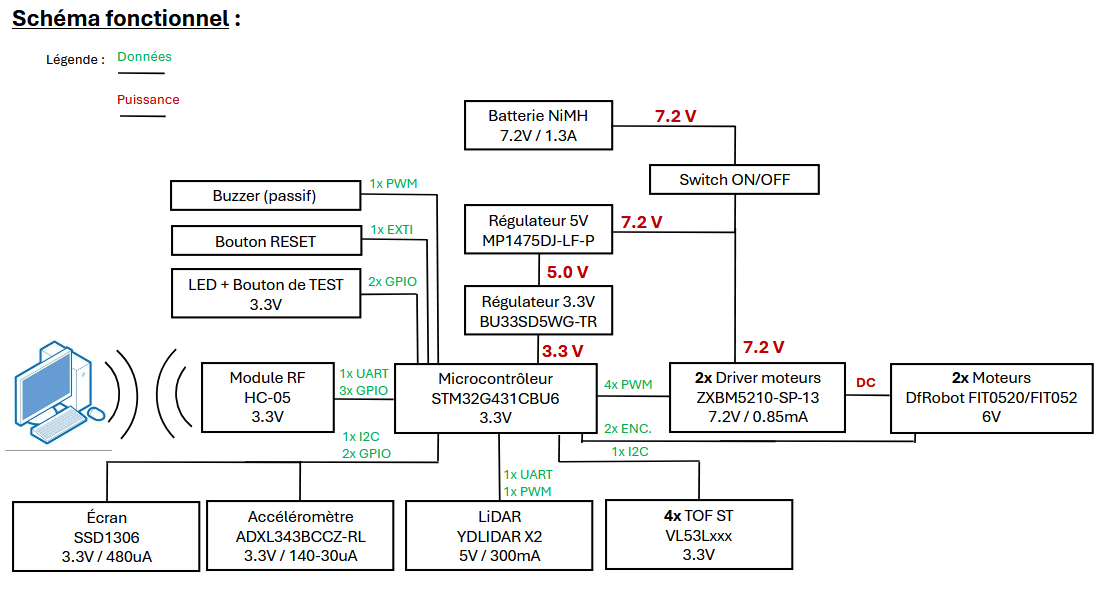
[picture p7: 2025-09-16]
Documents/Schéma fonctionnel.png

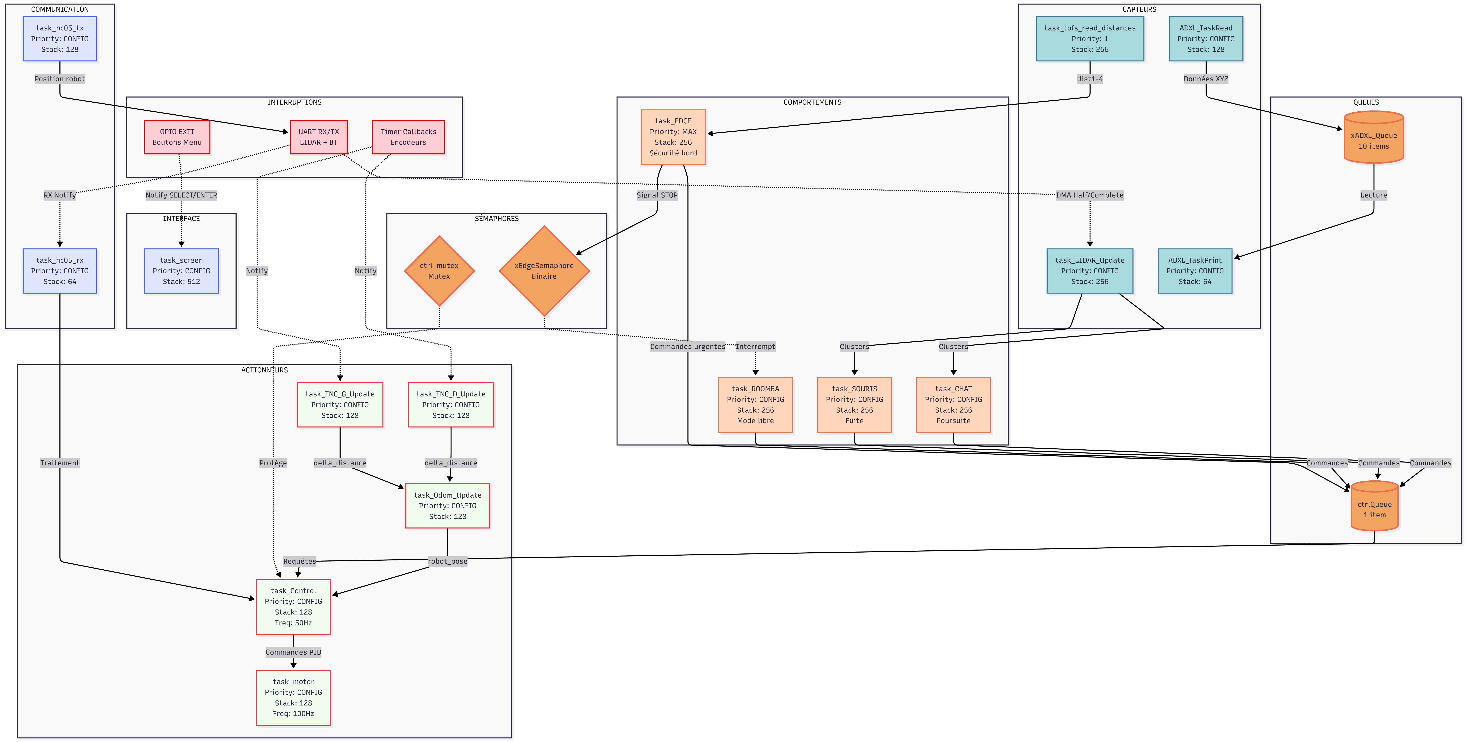
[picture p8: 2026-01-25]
Documents/Diagramme des taches.png

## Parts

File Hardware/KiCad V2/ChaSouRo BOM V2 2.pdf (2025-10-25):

### ChaSouRo

Reference | Value | Footprint | Qty
C1 | 4.7u | Capacitor_SMD:C_0402_1005Metric | 1
C2,C3,C4,C9,C10,C13,C15,C17,C18,C20,C23,C28,C29,C30,C32,C33,C34,C35,C36,C37 | 0.1u | Capacitor_SMD:C_0402_1005Metric | 20
C5 | 10n | Capacitor_SMD:C_0402_1005Metric | 1
C6,C8,C25,C26 | 1u | Capacitor_SMD:C_0402_1005Metric | 4
C7,C21,C22 | 22u | Capacitor_SMD:C_0603_1608Metric | 3
C11,C12 | 22p | Capacitor_SMD:C_0402_1005Metric | 2
C14,C16,C27,C31 | 10u | Capacitor_SMD:C_0603_1608Metric | 4
C19 | 47u | Capacitor_SMD:C_Elec_5x5.4 | 1
C24 | 15p | Capacitor_SMD:C_0402_1005Metric | 1
D1 | 1 | LED_SMD:LED_0603_1608Metric | 1
D2 | 2 | LED_SMD:LED_0603_1608Metric | 1
D3 | 3V3 | LED_SMD:LED_0603_1608Metric | 1
H1,H2,H3,H4 | MountingHole_Pad | MountingHole:MountingHole_3.2mm_M3_Pad_Via | 4
IC1 | ADXL343BCCZ-RL | ESE:ADXL343BCCZRL | 1
IC2,IC4 | ZXBM5210-SP-13 | ESE:SOIC127P600X150-9N | 2
IC3 | MP1475DJ-LF-P | Package_TO_SOT_SMD:TSOT-23-8 | 1
IC5 | BU33SD5WG-TR | ESE:SOT95P280X125-5N | 1
J1 | LiDAR | Connector_JST:JST_PH_S4B-PH-K_1x04_P2.00mm_Horizontal | 1
J2 | OLED | Connector_JST:JST_PH_S4B-PH-K_1x04_P2.00mm_Horizontal | 1
J3 | Conn_ST_STDC14 | Connector_PinHeader_1.27mm:PinHeader_2x07_P1.27mm_Vertical_SMD | 1
J4 | BT | Connector_PinHeader_2.54mm:PinHeader_1x06_P2.54mm_Vertical | 1
J5 | ToF1 | Connector_JST:JST_PH_S5B-PH-K_1x05_P2.00mm_Horizontal | 1
J6 | ToF2 | Connector_JST:JST_PH_S5B-PH-K_1x05_P2.00mm_Horizontal | 1
J7 | ToF3 | Connector_JST:JST_PH_S5B-PH-K_1x05_P2.00mm_Horizontal | 1
J8 | ToF4 | Connector_JST:JST_PH_S5B-PH-K_1x05_P2.00mm_Horizontal | 1
J9 | Motor_L | Connector_JST:JST_PH_S6B-PH-K_1x06_P2.00mm_Horizontal | 1
J10 | Motor_R | Connector_JST:JST_PH_S6B-PH-K_1x06_P2.00mm_Horizontal | 1
J11 | BATT + ON/OFF | Connector_JST:JST_PH_S4B-PH-K_1x04_P2.00mm_Horizontal | 1
J12 | Buzz | Connector_JST:JST_PH_S2B-PH-K_1x02_P2.00mm_Horizontal | 1
L1 | 4.7n | Inductor_SMD:L_0402_1005Metric | 1
L2 | 4.7u | Inductor_SMD:L_Wuerth_HCI-5040 | 1
Q1 | SQ2310ES | Package_TO_SOT_SMD:SOT-23 | 1
R1,R2,R13 | 2.7k | Resistor_SMD:R_0402_1005Metric | 3
R3,R4,R5,R6 | 4.7k | Resistor_SMD:R_0402_1005Metric | 4
R7 | 20 | Resistor_SMD:R_0402_1005Metric | 1
R8,R9,R14,R17,R18,R19,R20 | 100k | Resistor_SMD:R_0402_1005Metric | 7
R10 | 16k | Resistor_SMD:R_0402_1005Metric | 1
R11 | 40.2k | Resistor_SMD:R_0402_1005Metric | 1
R12 | 7.68k | Resistor_SMD:R_0402_1005Metric | 1
R15 | 470 | Resistor_SMD:R_0402_1005Metric | 1
R16 | 100 | Resistor_SMD:R_0402_1005Metric | 1
S1 | NRST | ESE:430182070816 | 1
S2 | USER | ESE:430182070816 | 1
TP1 | TX2 | | 1
TP2 | GND | TestPoint:TestPoint_Bridge_Pitch2.0mm_Drill0.7mm | 1
TP3 | 3V3 | TestPoint:TestPoint_Bridge_Pitch2.0mm_Drill0.7mm | 1
TP4 | FWD_L | TestPoint:TestPoint_Bridge_Pitch2.0mm_Drill0.7mm | 1
TP5 | REV_L | TestPoint:TestPoint_Bridge_Pitch2.0mm_Drill0.7mm | 1
TP6 | FWD_R | TestPoint:TestPoint_Bridge_Pitch2.0mm_Drill0.7mm | 1
TP7 | REV_R | TestPoint:TestPoint_Bridge_Pitch2.0mm_Drill0.7mm | 1
TP8 | USER2 | | 1
U1 | STM32G431CBUx | Package_DFN_QFN:QFN-48-1EP_7x7mm_P0.5mm_EP5.6x5.6mm | 1
Y1 | Crystal_GND24_Small | Crystal:Crystal_SMD_3225-4Pin_3.2x2.5mm | 1

1

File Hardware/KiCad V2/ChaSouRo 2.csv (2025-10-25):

Reference | Value | Footprint | Datasheet | Qty | DNP | Exclude from BOM | Exclude from Board
C1 | 4.7u | Capacitor_SMD:C_0402_1005Metric | ~ | 1
C2,C3,C4,C9,C10,C13,C15,C17,C18,C20,C23,C28,C29,C30,C32,C33,C34,C35,C36,C37 | 0.1u | Capacitor_SMD:C_0402_1005Metric | ~ | 20
C5 | 10n | Capacitor_SMD:C_0402_1005Metric | ~ | 1
C6,C8,C25,C26 | 1u | Capacitor_SMD:C_0402_1005Metric | ~ | 4
C7,C21,C22 | 22u | Capacitor_SMD:C_0603_1608Metric | ~ | 3
C11,C12 | 22p | Capacitor_SMD:C_0402_1005Metric | ~ | 2
C14,C16,C27,C31 | 10u | Capacitor_SMD:C_0603_1608Metric | ~ | 4
C19 | 47u | Capacitor_SMD:C_Elec_5x5.4 | ~ | 1
C24 | 15p | Capacitor_SMD:C_0402_1005Metric | ~ | 1
D1 | 1 | LED_SMD:LED_0603_1608Metric | ~ | 1
D2 | 2 | LED_SMD:LED_0603_1608Metric | ~ | 1
D3 | 3V3 | LED_SMD:LED_0603_1608Metric | ~ | 1
H1,H2,H3,H4 | MountingHole_Pad | MountingHole:MountingHole_3.2mm_M3_Pad_Via | ~ | 4 |  | Exclure de la Liste du Matériel
IC1 | ADXL343BCCZ-RL | ESE:ADXL343BCCZRL | https://www.analog.com/media/en/technical-documentation/data-sheets/ADXL343.pdf | 1
IC2,IC4 | ZXBM5210-SP-13 | ESE:SOIC127P600X150-9N | https://www.diodes.com/assets/Datasheets/ZXBM5210.pdf | 2
IC3 | MP1475DJ-LF-P | Package_TO_SOT_SMD:TSOT-23-8 | https://www.monolithicpower.com/en/documentview/productdocument/index/version/2/document_type/Datasheet/lang/en/sku/MP1475/document_id/342 | 1
IC5 | BU33SD5WG-TR | ESE:SOT95P280X125-5N | https://componentsearchengine.com/Datasheets/1/BU33SD5WG-TR.pdf | 1
J1 | LiDAR | Connector_JST:JST_PH_S4B-PH-K_1x04_P2.00mm_Horizontal | ~ | 1
J2 | OLED | Connector_JST:JST_PH_S4B-PH-K_1x04_P2.00mm_Horizontal | ~ | 1
J3 | Conn_ST_STDC14 | Connector_PinHeader_1.27mm:PinHeader_2x07_P1.27mm_Vertical_SMD | https://www.st.com/content/ccc/resource/technical/document/user_manual/group1/99/49/91/b6/b2/3a/46/e5/DM00526767/files/DM00526767.pdf/jcr:content/translations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 | 1
J4 | BT | Connector_PinHeader_2.54mm:PinHeader_1x06_P2.54mm_Vertical | ~ | 1
J5 | ToF1 | Connector_JST:JST_PH_S5B-PH-K_1x05_P2.00mm_Horizontal | ~ | 1
J6 | ToF2 | Connector_JST:JST_PH_S5B-PH-K_1x05_P2.00mm_Horizontal | ~ | 1
J7 | ToF3 | Connector_JST:JST_PH_S5B-PH-K_1x05_P2.00mm_Horizontal | ~ | 1
J8 | ToF4 | Connector_JST:JST_PH_S5B-PH-K_1x05_P2.00mm_Horizontal | ~ | 1
J9 | Motor_L | Connector_JST:JST_PH_S6B-PH-K_1x06_P2.00mm_Horizontal | ~ | 1
J10 | Motor_R | Connector_JST:JST_PH_S6B-PH-K_1x06_P2.00mm_Horizontal | ~ | 1
J11 | BATT + ON/OFF | Connector_JST:JST_PH_S4B-PH-K_1x04_P2.00mm_Horizontal | ~ | 1
J12 | Buzz | Connector_JST:JST_PH_S2B-PH-K_1x02_P2.00mm_Horizontal | ~ | 1
L1 | 4.7n | Inductor_SMD:L_0402_1005Metric | ~ | 1
L2 | 4.7u | Inductor_SMD:L_Wuerth_HCI-5040 | ~ | 1
Q1 | SQ2310ES | Package_TO_SOT_SMD:SOT-23 | https://docs.rs-online.com/62ad/0900766b8126cf20.pdf | 1
R1,R2,R13 | 2.7k | Resistor_SMD:R_0402_1005Metric | ~ | 3
R3,R4,R5,R6 | 4.7k | Resistor_SMD:R_0402_1005Metric | ~ | 4
R7 | 20 | Resistor_SMD:R_0402_1005Metric | ~ | 1
R8,R9,R14,R17,R18,R19,R20 | 100k | Resistor_SMD:R_0402_1005Metric | ~ | 7
R10 | 16k | Resistor_SMD:R_0402_1005Metric | ~ | 1
R11 | 40.2k | Resistor_SMD:R_0402_1005Metric | ~ | 1
R12 | 7.68k | Resistor_SMD:R_0402_1005Metric | ~ | 1
R15 | 470 | Resistor_SMD:R_0402_1005Metric | ~ | 1
R16 | 100 | Resistor_SMD:R_0402_1005Metric | ~ | 1
S1 | NRST | ESE:430182070816 | ~ | 1
S2 | USER | ESE:430182070816 | ~ | 1
TP1 | TX2 |  | ~ | 1
TP2 | GND | TestPoint:TestPoint_Bridge_Pitch2.0mm_Drill0.7mm | ~ | 1
TP3 | 3V3 | TestPoint:TestPoint_Bridge_Pitch2.0mm_Drill0.7mm | ~ | 1
TP4 | FWD_L | TestPoint:TestPoint_Bridge_Pitch2.0mm_Drill0.7mm | ~ | 1
TP5 | REV_L | TestPoint:TestPoint_Bridge_Pitch2.0mm_Drill0.7mm | ~ | 1
TP6 | FWD_R | TestPoint:TestPoint_Bridge_Pitch2.0mm_Drill0.7mm | ~ | 1
TP7 | REV_R | TestPoint:TestPoint_Bridge_Pitch2.0mm_Drill0.7mm | ~ | 1
TP8 | USER2 |  | ~ | 1
U1 | STM32G431CBUx | Package_DFN_QFN:QFN-48-1EP_7x7mm_P0.5mm_EP5.6x5.6mm | https://www.st.com/resource/en/datasheet/stm32g431cb.pdf | 1
Y1 | Crystal_GND24_Small | Crystal:Crystal_SMD_3225-4Pin_3.2x2.5mm | ~ | 1

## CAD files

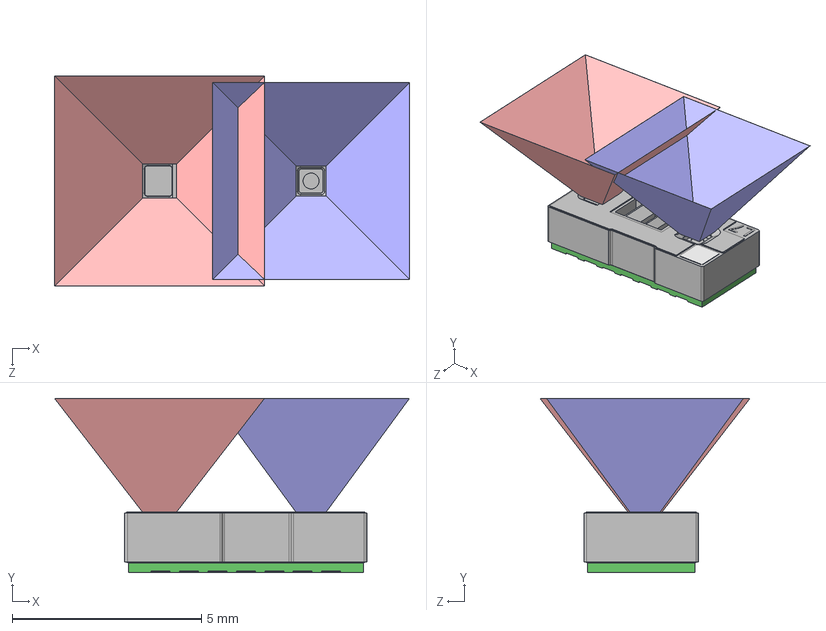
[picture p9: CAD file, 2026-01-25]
Hardware/CAO & Symboles/3D/VL53L7 3D Model.step
9.37 x 4.60 x 5.55 mm
VL53L7_SUBSTRATE_Customer Model
VL53L7 CAP_Customer Model
VL53L7_Tx Exclusion Cone_Tx Exclusion Cone
VL53L7_Rx Exclusion Cone_Rx Exclusion Zone

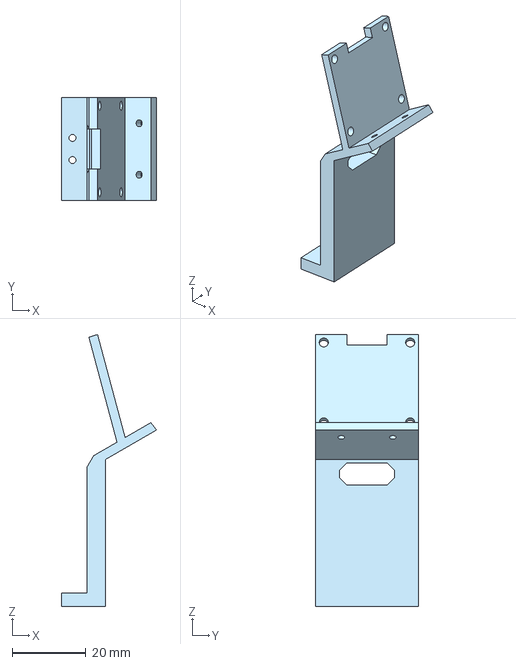
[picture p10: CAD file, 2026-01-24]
Mecanique/Support ecran.3mf
25.9 x 28.0 x 74.0 mm

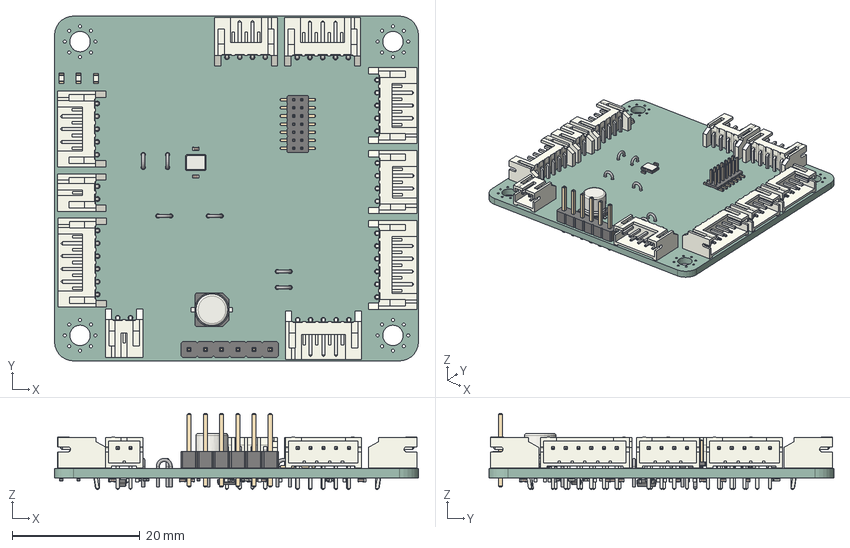
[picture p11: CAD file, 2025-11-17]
Hardware/Logo/ChaSouRo.step
57.0 x 54.0 x 11.9 mm
C_Elec_5x5.4
JST_PH_S5B-PH-K_1x05_P2.00mm_Horizontal x 4
TestPoint_Bridge_Pitch2.0mm_Drill0.7mm x 6
LED_0603_1608Metric x 3
JST_PH_S2B-PH-K_1x02_P2.00mm_Horizontal x 2
JST_PH_S6B-PH-K_1x06_P2.00mm_Horizontal x 2
Crystal_SMD_3225-4Pin_3.2x2.5mm
C_0402_1005Metric x 34
PinHeader_2x07_P1.27mm_Vertical_SMD
JST_PH_S4B-PH-K_1x04_P2.00mm_Horizontal x 2
PinHeader_1x06_P2.54mm_Vertical
R_0402_1005Metric x 20
SOT-23
L_0402_1005Metric
TSOT-23-8
ChaSouRo_PCB

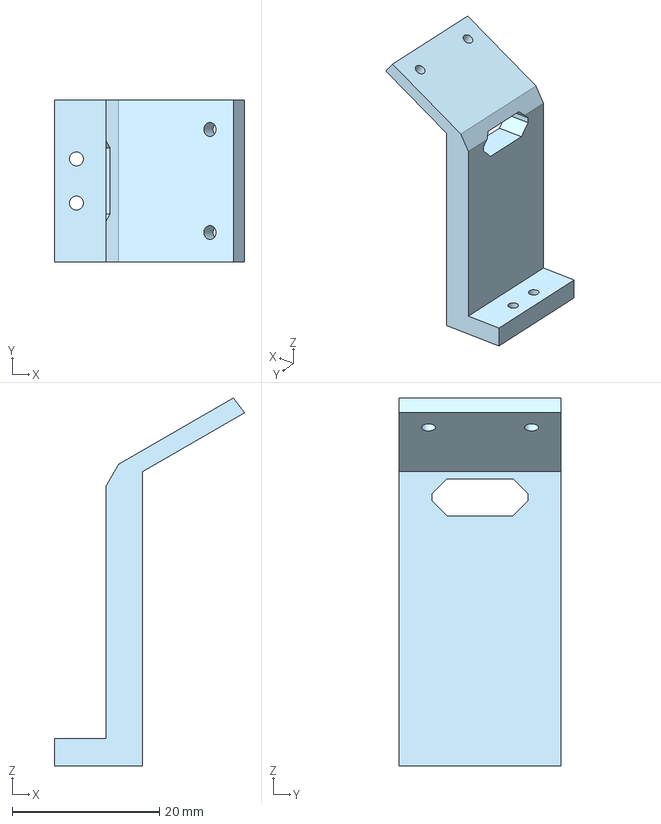
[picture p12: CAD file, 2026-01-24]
Mecanique/Support TOF.3mf
25.9 x 22.0 x 50.0 mm

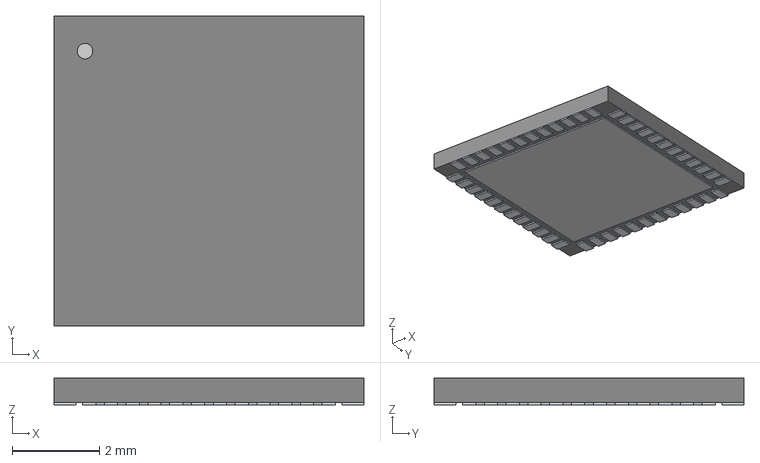
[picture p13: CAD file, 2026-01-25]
Hardware/CAO & Symboles/3D/UFQFPN-48_7X7X0P55MM.step
7.11 x 7.11 x 0.612 mm

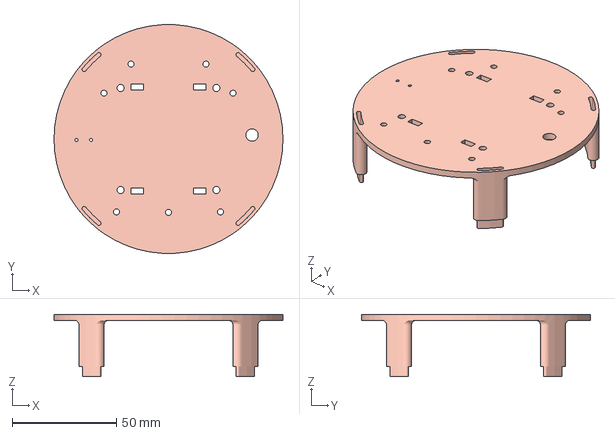
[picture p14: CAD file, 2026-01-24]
Mecanique/Tower - Parts sup.3mf
110.0 x 109.8 x 30.0 mm

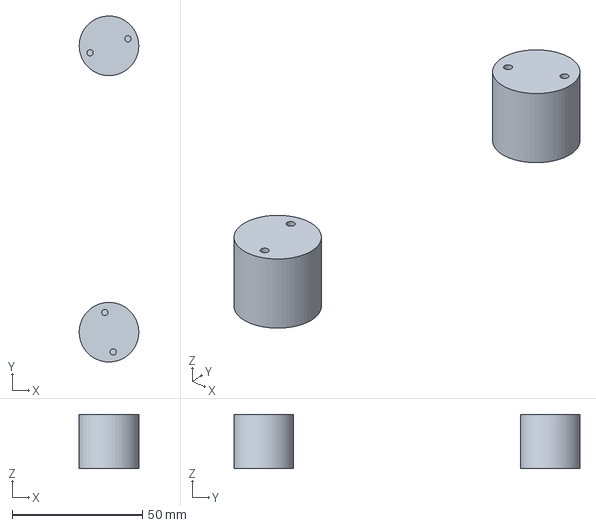
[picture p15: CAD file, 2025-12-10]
Mecanique/Robot 3mf.3mf
22.9 x 132.9 x 20.9 mm

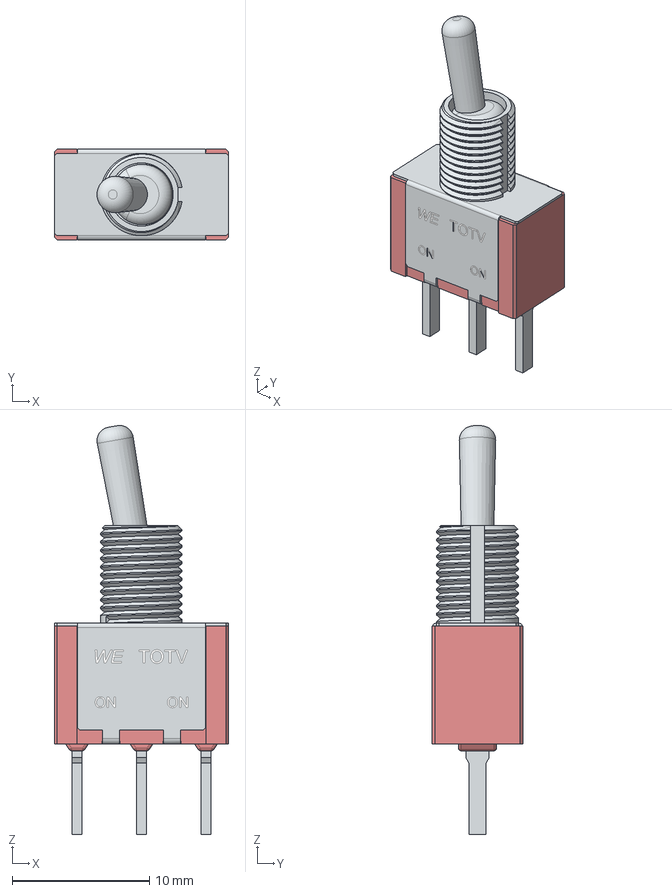
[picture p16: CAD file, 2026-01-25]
Hardware/CAO & Symboles/3D/STP_472121020311_rev1.stp
12.7 x 6.60 x 29.8 mm
Base
Shielding
Switch
Pin x 3
Glue x 3

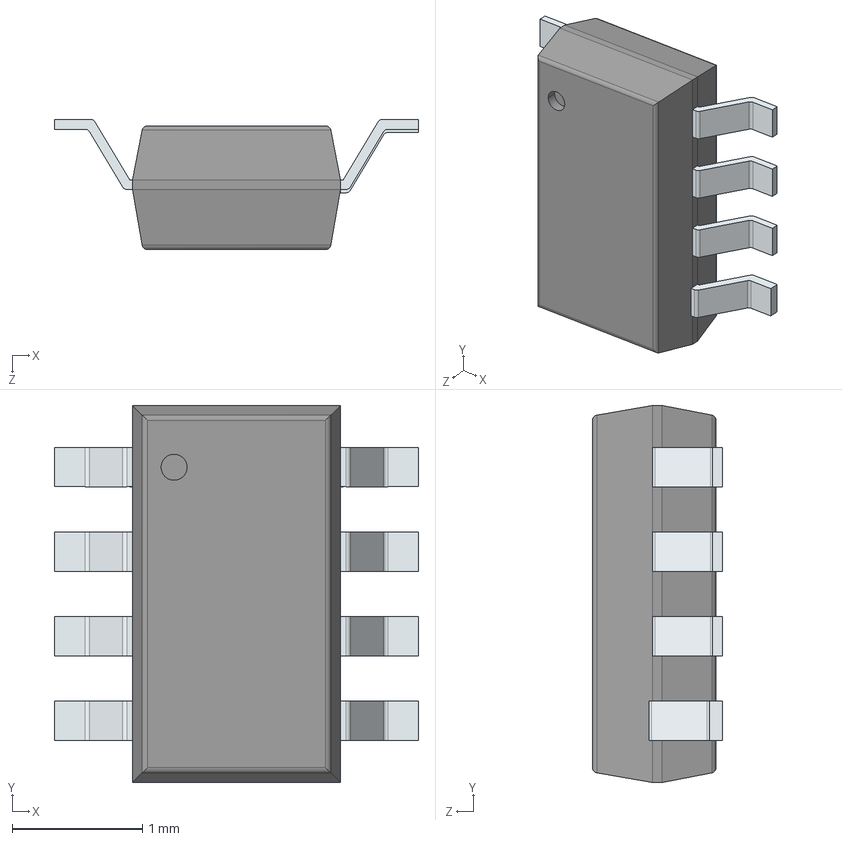
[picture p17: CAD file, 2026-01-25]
Hardware/CAO & Symboles/3D/MP1475DJ-LF-P.stp
2.80 x 2.90 x 1.00 mm
PinsArrayLR_2
PinsArrayLR_5
PinsArrayLR_1
PinsArrayLR
PinsArrayLR_6
PinsArrayLR_7
PinsArrayLR_3
PinsArrayLR_4

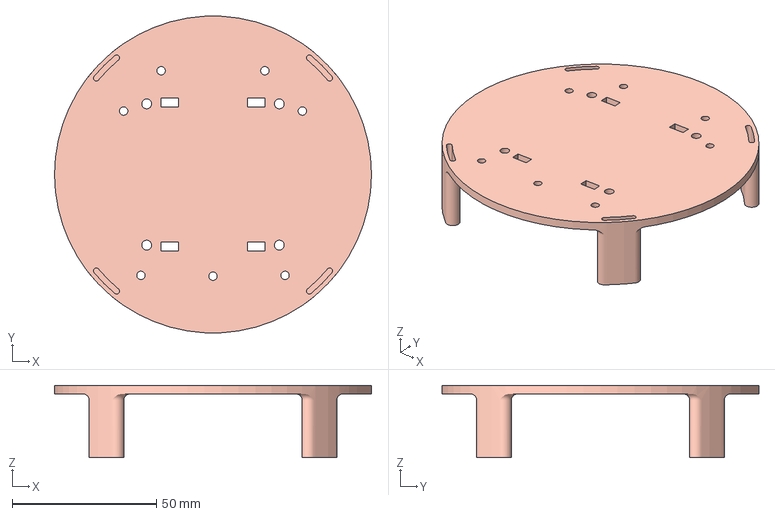
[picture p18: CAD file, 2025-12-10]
Mecanique/Tower Parts Robot.3mf
110.0 x 109.8 x 25.0 mm

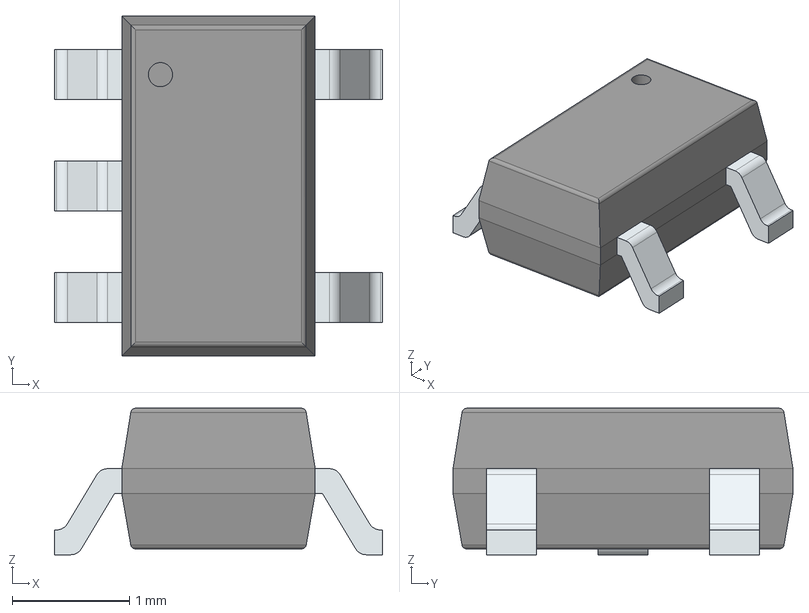
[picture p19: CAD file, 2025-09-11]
Hardware/CAO & Symboles/3D/BU33SD5WG-TR.stp
2.80 x 2.90 x 1.25 mm
PinsArrayL
PinsArrayR

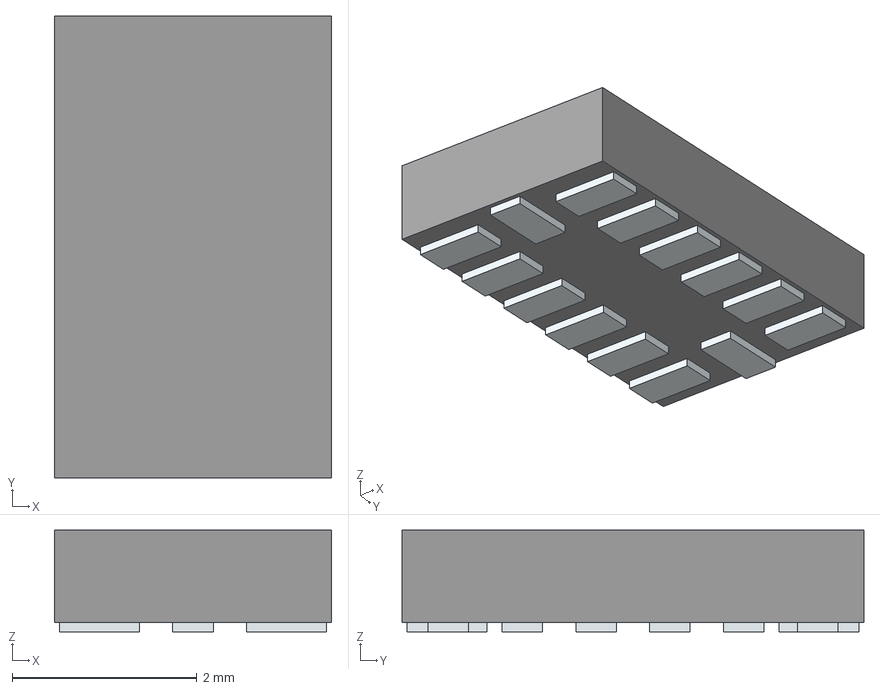
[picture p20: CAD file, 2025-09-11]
Hardware/CAO & Symboles/3D/ADXL343BCCZ-RL.stp
3.00 x 5.00 x 1.10 mm
Pins

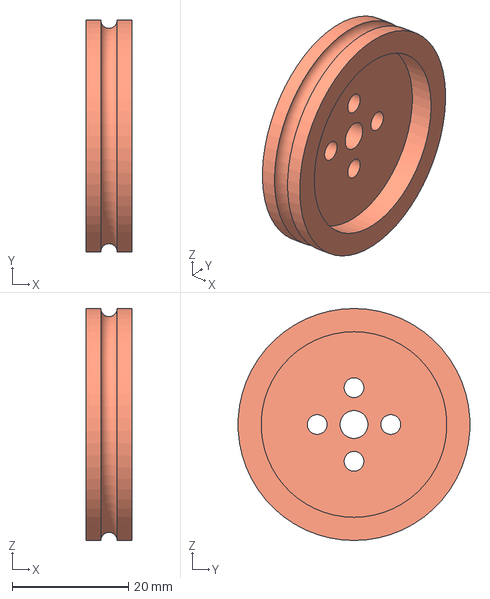
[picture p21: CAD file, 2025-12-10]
Mecanique/Wheels Robot.3mf
8.00 x 39.9 x 40.0 mm

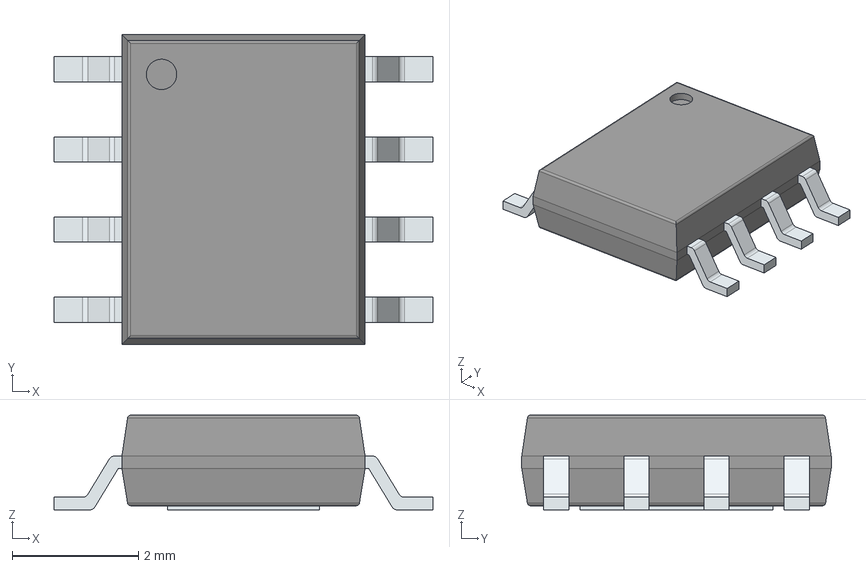
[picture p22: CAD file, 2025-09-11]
Hardware/CAO & Symboles/3D/ZXBM5210-SP-13.stp
6.00 x 4.90 x 1.50 mm
PinsArrayLR
ThermalPad

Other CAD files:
Hardware/Logo/support_silkscreen.SLDASM
Mecanique/ChaSouRo Robot Support.gcode.3mf
Mecanique/Wheels Robot.gcode.3mf
Mecanique/ChaSouRo Robot Support.3mf
Hardware/CAO & Symboles/3D/430182070816.stp
Hardware/CAO & Symboles/3D/M50-3600742.stp
Hardware/Logo/support_silkscreen.SLDPRT
Hardware/Logo/support_silkscreen.STL
Mecanique/Robot Parts Top.3mf
Mecanique/Robot Parts Top.gcode.3mf
Mecanique/Tower Parts Robot.gcode.3mf

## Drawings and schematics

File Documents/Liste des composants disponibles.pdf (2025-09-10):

## Liste des composants disponibles

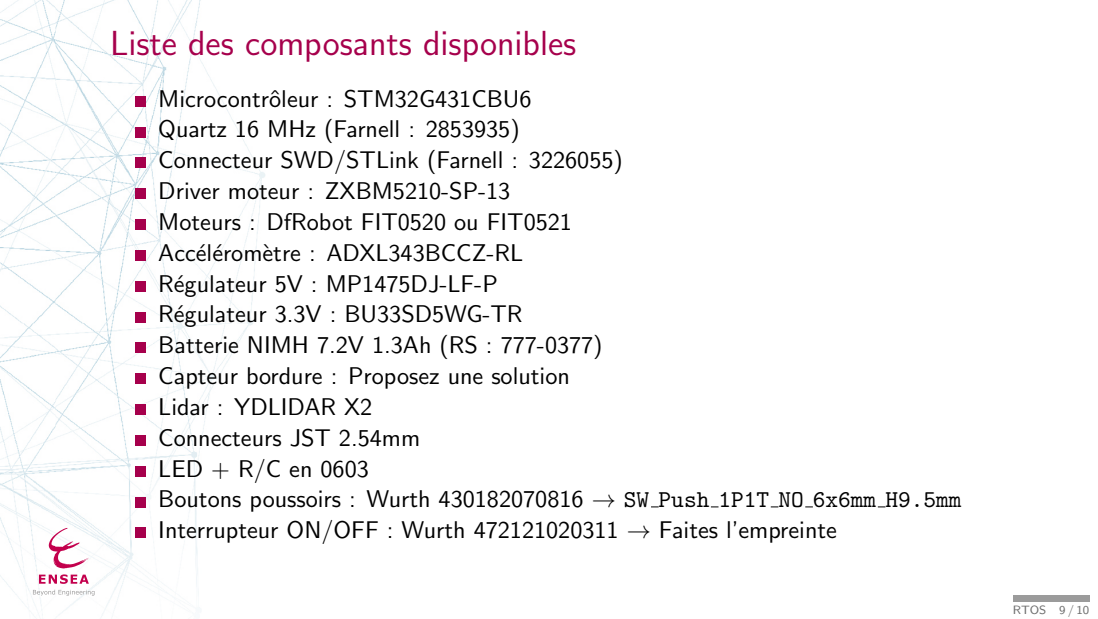
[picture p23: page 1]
RTOS 9 / 10

Microcontrˆoleur : STM32G431CBU6
Quartz 16 MHz (Farnell : 2853935)
Connecteur SWD/STLink (Farnell : 3226055)
Driver moteur : ZXBM5210-SP-13
Moteurs : DfRobot FIT0520 ou FIT0521
Acc´el´erom`etre : ADXL343BCCZ-RL
R´egulateur 5V : MP1475DJ-LF-P
R´egulateur 3.3V : BU33SD5WG-TR
Batterie NIMH 7.2V 1.3Ah (RS : 777-0377)
Capteur bordure : Proposez une solution
Lidar : YDLIDAR X2
Connecteurs JST 2.54mm
LED + R/C en 0603
Boutons poussoirs : Wurth 430182070816 → SW Push 1P1T NO 6x6mm H9.5mm
Interrupteur ON/OFF : Wurth 472121020311 → Faites l’empreinte

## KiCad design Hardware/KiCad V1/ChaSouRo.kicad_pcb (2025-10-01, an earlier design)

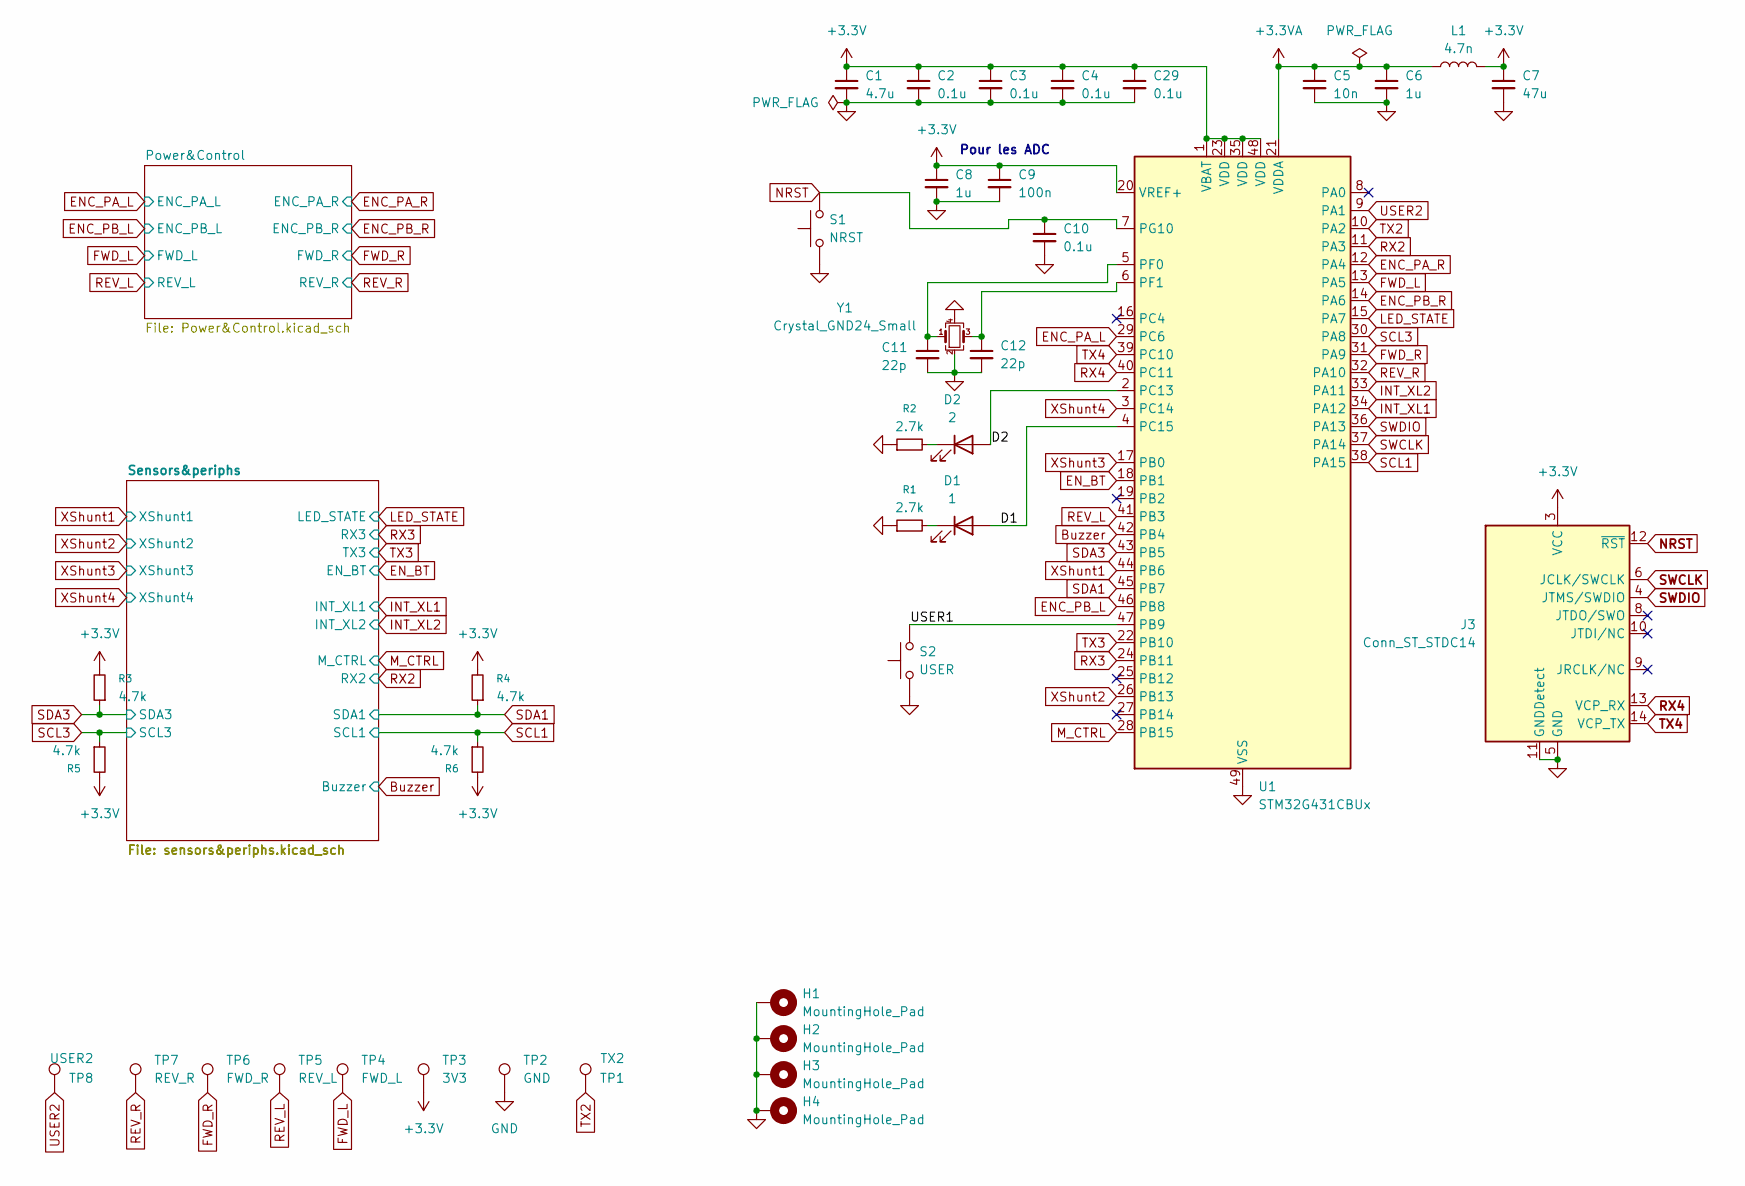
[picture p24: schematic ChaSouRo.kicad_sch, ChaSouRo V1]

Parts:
C1: 4.7u; C_0402_1005Metric
C2, C3, C4, C10, C29: 0.1u; C_0402_1005Metric
C5: 10n; C_0402_1005Metric
C6, C8: 1u; C_0402_1005Metric
C7: 47u; C_0402_1005Metric
C9: 100n; C_0402_1005Metric
C11, C12: 22p; C_0402_1005Metric
D1: 1; LED_0603_1608Metric
D2: 2; LED_0603_1608Metric
H1, H2, H3, H4: MountingHole_Pad; MountingHole_3.2mm_M3_Pad_Via
J3: Conn_ST_STDC14; PinHeader_2x07_P1.27mm_Vertical_SMD
L1: 4.7n; L_0402_1005Metric
R1, R2: 2.7k; R_0402_1005Metric
R3, R4, R5, R6: 4.7k; R_0402_1005Metric
S1: NRST; 430182070816
S2: USER; 430182070816
TP1: TX2
TP2: GND; TestPoint_Bridge_Pitch2.0mm_Drill0.7mm
TP3: 3V3; TestPoint_Bridge_Pitch2.0mm_Drill0.7mm
TP4: FWD_L; TestPoint_Bridge_Pitch2.0mm_Drill0.7mm
TP5: REV_L; TestPoint_Bridge_Pitch2.0mm_Drill0.7mm
TP6: FWD_R; TestPoint_Bridge_Pitch2.0mm_Drill0.7mm
TP7: REV_R; TestPoint_Bridge_Pitch2.0mm_Drill0.7mm
TP8: USER2
U1: STM32G431CBUx; QFN-48-1EP_7x7mm_P0.5mm_EP5.6x5.6mm
Y1: Crystal_GND24_Small; Crystal_SMD_3225-4Pin_3.2x2.5mm

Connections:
+3.3V: C1.1, C2.1, C3.1, C4.1, C7.1, C8.1, C9.1, C29.1, J3.3 (VCC), L1.2, R3.2, R4.2, R5.2, R6.2, TP3.1, U1.1 (VBAT), U1.20 (VREF+), U1.23 (VDD), U1.35 (VDD), U1.48 (VDD); also elsewhere on the board
+3.3VA: C5.1, C6.1, L1.1, U1.21 (VDDA)
/D1: D1.2 (A), U1.4 (PC15)
/D2: D2.2 (A), U1.2 (PC13)
/USER1: S2.2, U1.47 (PB9)
Buzzer: U1.42 (PB4); also elsewhere on the board
ENC_PA_L: U1.29 (PC6); also elsewhere on the board
ENC_PA_R: U1.12 (PA4); also elsewhere on the board
ENC_PB_L: U1.46 (PB8); also elsewhere on the board
ENC_PB_R: U1.14 (PA6); also elsewhere on the board
EN_BT: U1.18 (PB1); also elsewhere on the board
FWD_L: TP4.1, U1.13 (PA5); also elsewhere on the board
FWD_R: TP6.1, U1.31 (PA9); also elsewhere on the board
GND: C1.2, C2.2, C3.2, C4.2, C5.2, C6.2, C7.2, C8.2, C9.2, C10.2, C11.2, C12.2, C29.2, H1.1, H2.1, H3.1, H4.1, J3.5 (GND), J3.7 (GND), J3.11 (GNDDetect), R1.1, R2.1, S1.1, S2.1, TP2.1, U1.49 (VSS), Y1.2, Y1.4; also elsewhere on the board
INT_XL1: U1.34 (PA12); also elsewhere on the board
INT_XL2: U1.33 (PA11); also elsewhere on the board
LED_STATE: U1.15 (PA7); also elsewhere on the board
M_CTRL: U1.28 (PB15); also elsewhere on the board
NRST: C10.1, J3.12 (~RST), S1.2, U1.7 (PG10)
unnamed: D1.1 (K), R1.2
unnamed: D2.1 (K), R2.2
unnamed: C11.1, U1.5 (PF0), Y1.1
unnamed: C12.1, U1.6 (PF1), Y1.3
REV_L: TP5.1, U1.41 (PB3); also elsewhere on the board
REV_R: TP7.1, U1.32 (PA10); also elsewhere on the board
RX2: U1.11 (PA3); also elsewhere on the board
RX3: U1.24 (PB11); also elsewhere on the board
RX4: J3.13 (VCP_RX), U1.40 (PC11)
SCL1: R6.1, U1.38 (PA15); also elsewhere on the board
SCL3: R5.1, U1.30 (PA8); also elsewhere on the board
SDA1: R4.1, U1.45 (PB7); also elsewhere on the board
SDA3: R3.1, U1.43 (PB5); also elsewhere on the board
SWCLK: J3.6 (JCLK/SWCLK), U1.37 (PA14)
SWDIO: J3.4 (JTMS/SWDIO), U1.36 (PA13)
TX2: TP1.1, U1.10 (PA2)
TX3: U1.22 (PB10); also elsewhere on the board
TX4: J3.14 (VCP_TX), U1.39 (PC10)
USER2: TP8.1, U1.9 (PA1)
XShunt1: U1.44 (PB6); also elsewhere on the board
XShunt2: U1.26 (PB13); also elsewhere on the board
XShunt3: U1.17 (PB0); also elsewhere on the board
XShunt4: U1.3 (PC14); also elsewhere on the board

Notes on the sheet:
Pour les ADC

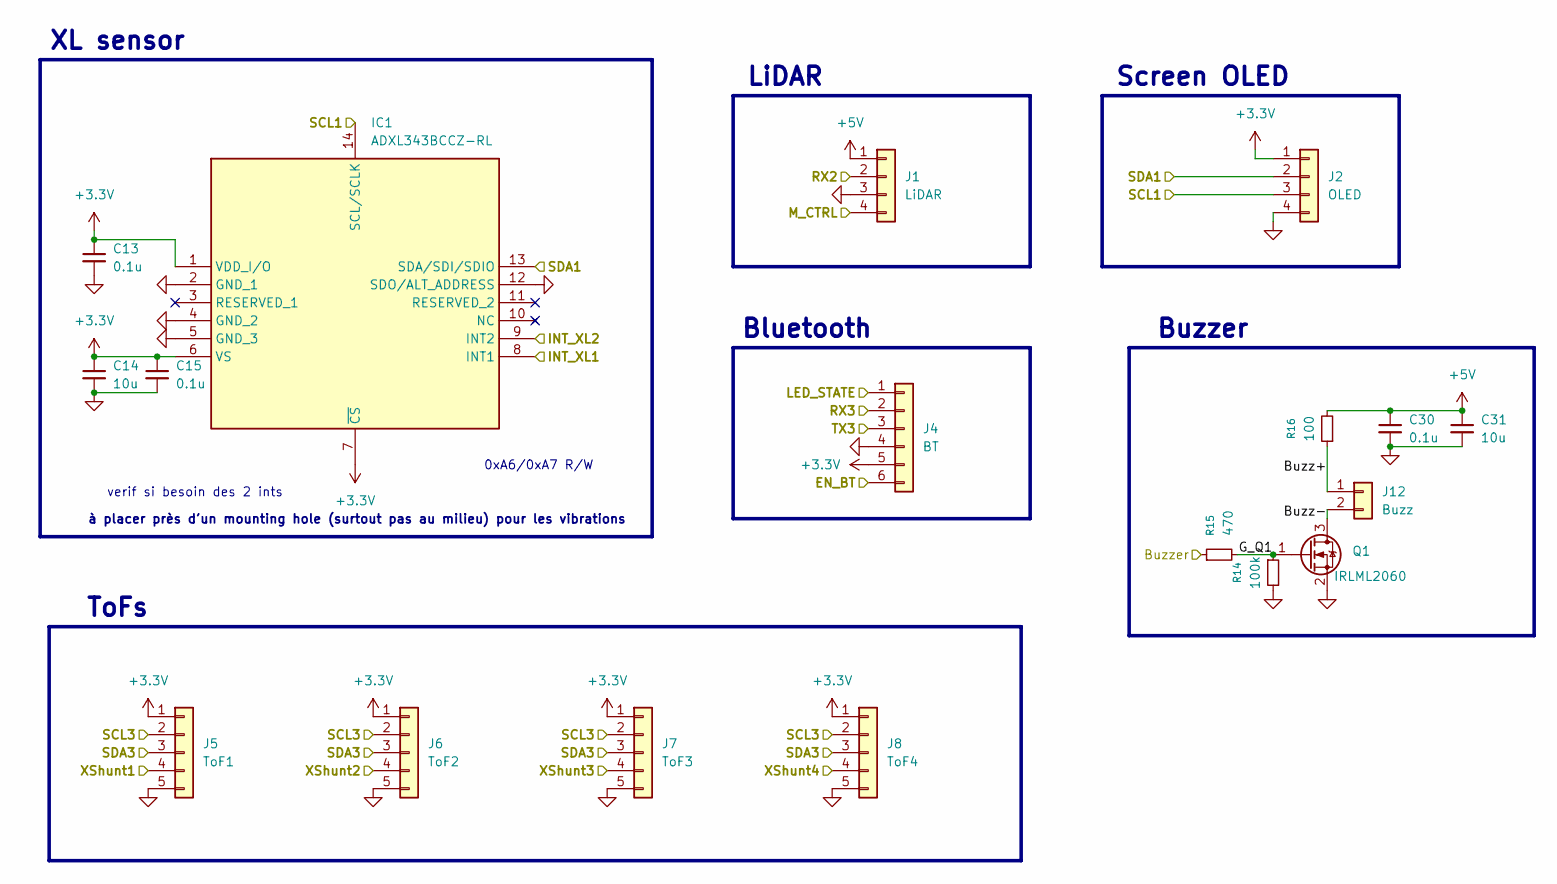
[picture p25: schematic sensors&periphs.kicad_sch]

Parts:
C13, C15, C30: 0.1u; C_0402_1005Metric
C14, C31: 10u; C_0402_1005Metric
IC1: ADXL343BCCZ-RL; ADXL343BCCZRL; Manufacturer_Part_Number ADXL343BCCZ-RL
J1: LiDAR; JST_PH_S4B-PH-K_1x04_P2.00mm_Horizontal
J2: OLED; JST_PH_S4B-PH-K_1x04_P2.00mm_Horizontal
J4: BT; PinHeader_1x06_P2.54mm_Vertical
J5: ToF1; JST_PH_S5B-PH-K_1x05_P2.00mm_Horizontal
J6: ToF2; JST_PH_S5B-PH-K_1x05_P2.00mm_Horizontal
J7: ToF3; JST_PH_S5B-PH-K_1x05_P2.00mm_Horizontal
J8: ToF4; JST_PH_S5B-PH-K_1x05_P2.00mm_Horizontal
J12: Buzz; JST_PH_S2B-PH-K_1x02_P2.00mm_Horizontal
Q1: IRLML2060; SOT-23
R14: 100k; R_0402_1005Metric
R15: 470; R_0402_1005Metric
R16: 100; R_0402_1005Metric

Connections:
+3.3V: C13.1, C14.1, C15.1, IC1.1 (VDD_I/O), IC1.6 (VS), IC1.7 (~CS), J2.1, J4.5, J5.1, J6.1, J7.1, J8.1; also elsewhere on the board
+5V: C30.1, C31.1, J1.1, R16.2; also elsewhere on the board
/Sensors&periphs/Buzz+: J12.1, R16.1
/Sensors&periphs/Buzz-: J12.2, Q1.3 (D)
/Sensors&periphs/G_Q1: Q1.1 (G), R14.1, R15.2
Buzzer: R15.1; also elsewhere on the board
EN_BT: J4.6; also elsewhere on the board
GND: C13.2, C14.2, C15.2, C30.2, C31.2, IC1.2 (GND_1), IC1.4 (GND_2), IC1.5 (GND_3), IC1.12 (SDO/ALT_ADDRESS), J1.3, J2.4, J4.4, J5.5, J6.5, J7.5, J8.5, Q1.2 (S), R14.2; also elsewhere on the board
INT_XL1: IC1.8 (INT1); also elsewhere on the board
INT_XL2: IC1.9 (INT2); also elsewhere on the board
LED_STATE: J4.1; also elsewhere on the board
M_CTRL: J1.4; also elsewhere on the board
RX2: J1.2; also elsewhere on the board
RX3: J4.2; also elsewhere on the board
SCL1: IC1.14 (SCL/SCLK), J2.3; also elsewhere on the board
SCL3: J5.2, J6.2, J7.2, J8.2; also elsewhere on the board
SDA1: IC1.13 (SDA/SDI/SDIO), J2.2; also elsewhere on the board
SDA3: J5.3, J6.3, J7.3, J8.3; also elsewhere on the board
TX3: J4.3; also elsewhere on the board
XShunt1: J5.4; also elsewhere on the board
XShunt2: J6.4; also elsewhere on the board
XShunt3: J7.4; also elsewhere on the board
XShunt4: J8.4; also elsewhere on the board

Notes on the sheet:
Screen OLED
LiDAR
à placer près d'un mounting hole (surtout pas au milieu) pour les vibrations
XL sensor
ToFs
verif si besoin des 2 ints
Buzzer
0xA6/0xA7 R/W
Bluetooth

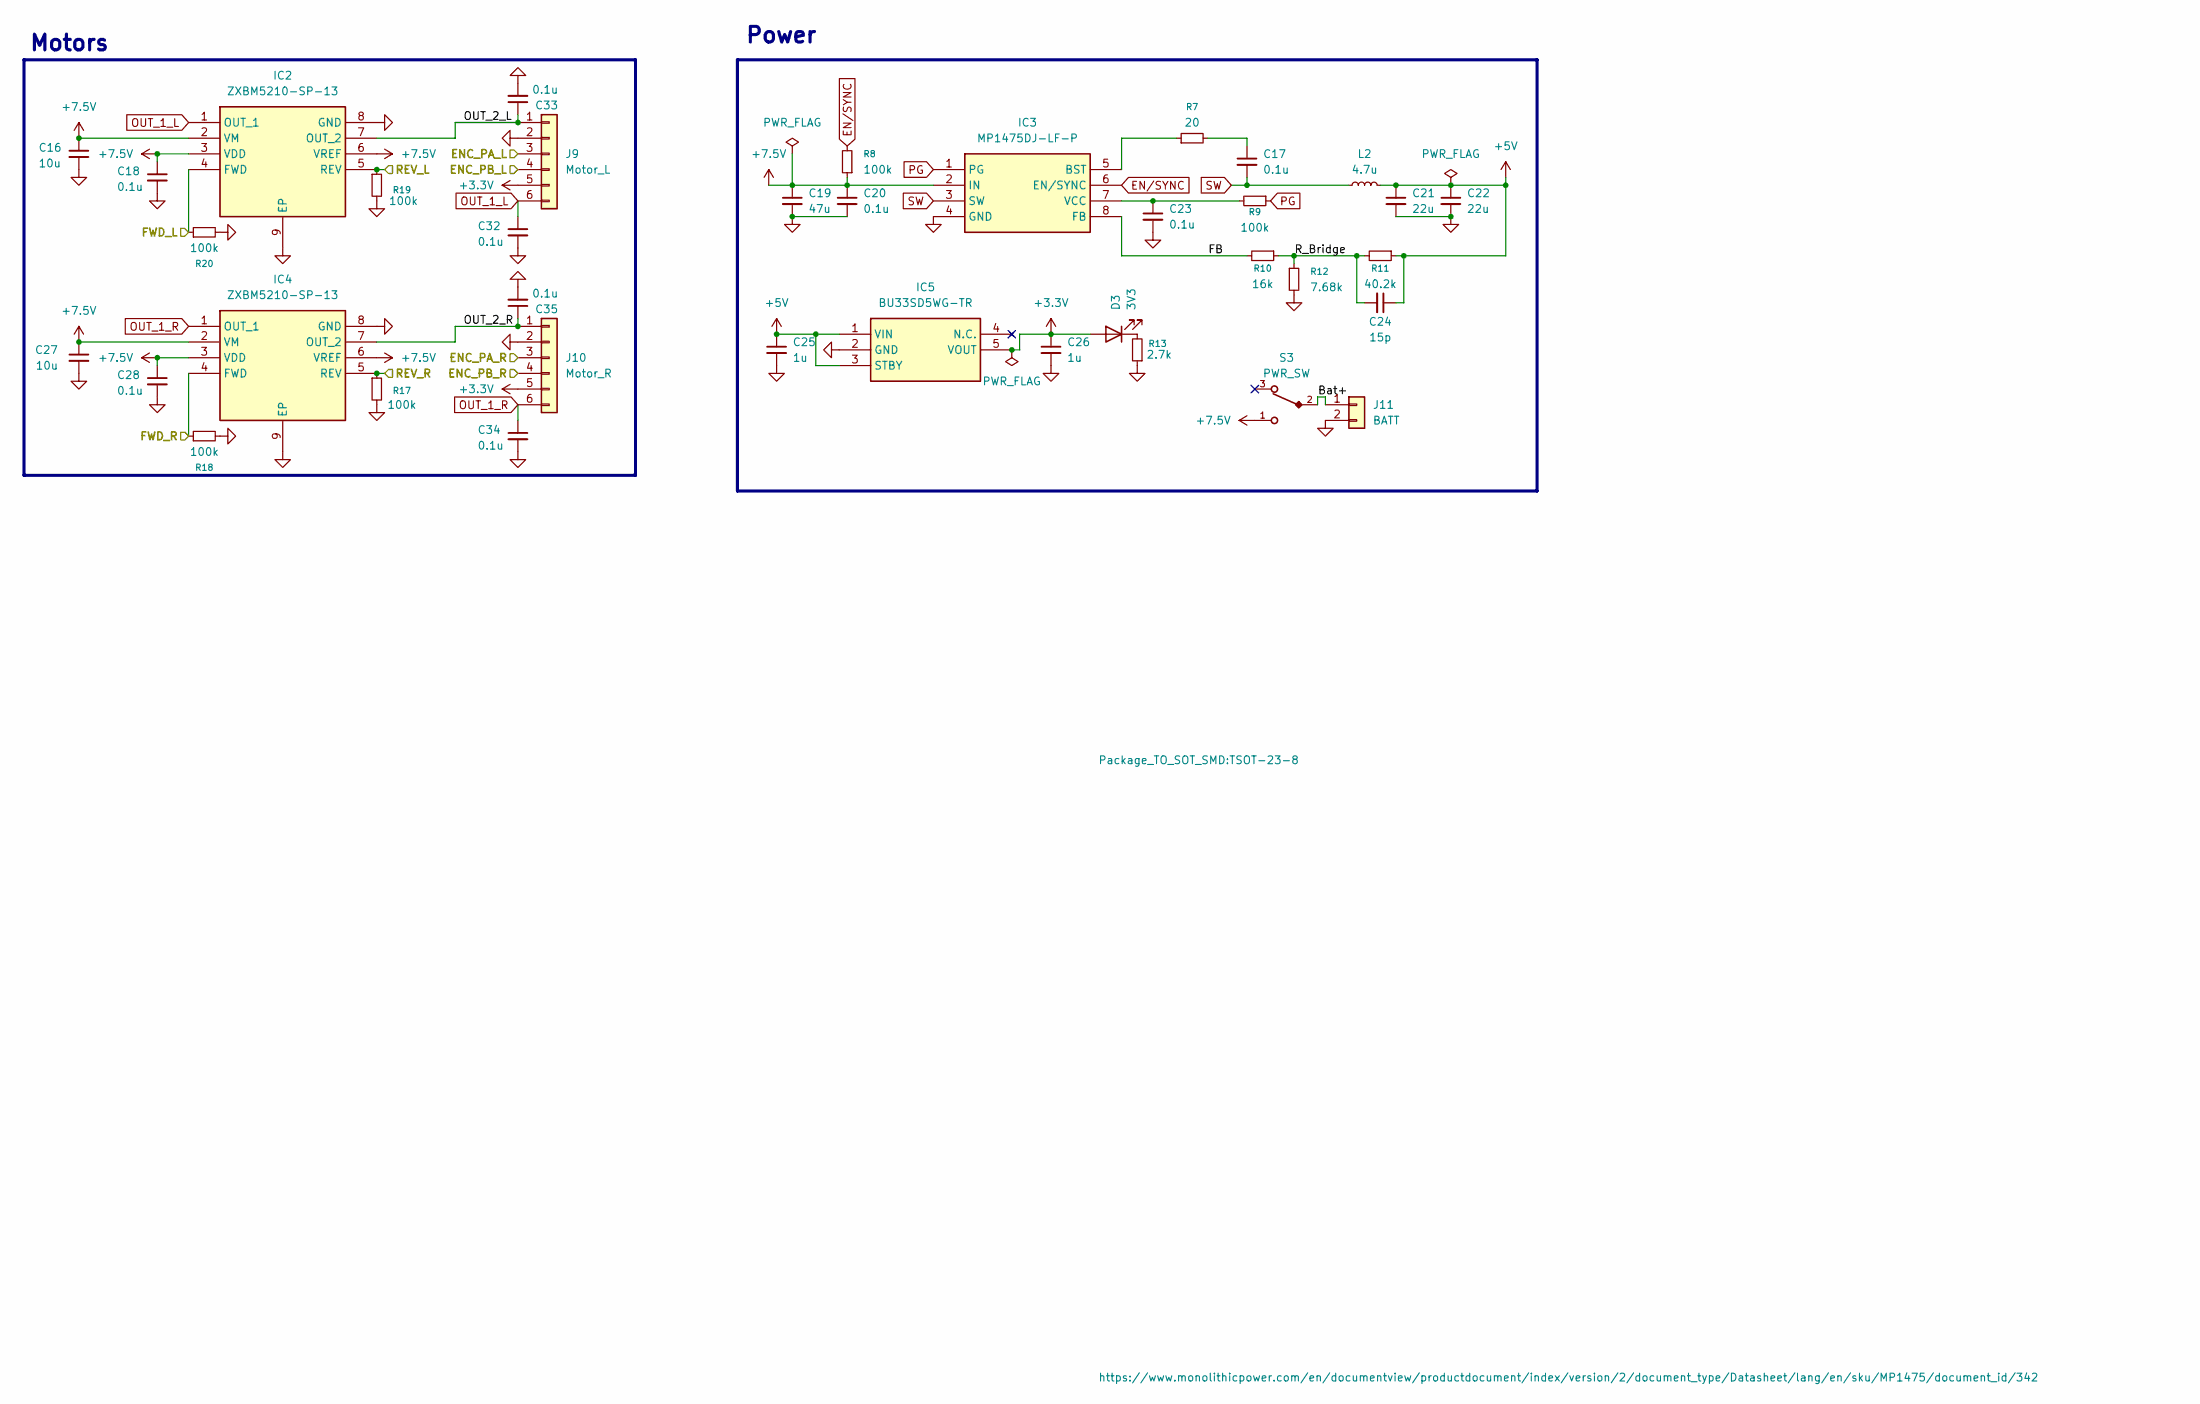
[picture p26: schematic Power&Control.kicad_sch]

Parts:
C16, C27: 10u; C_0402_1005Metric
C17, C18, C20, C23, C28, C32, C33, C34, C35: 0.1u; C_0402_1005Metric
C19: 47u; C_Elec_5x5.4
C21, C22: 22u; C_0402_1005Metric
C24: 15p; C_0402_1005Metric
C25, C26: 1u; C_0402_1005Metric
D3: 3V3; LED_0603_1608Metric
IC2, IC4: ZXBM5210-SP-13; SOIC127P600X150-9N; Manufacturer_Part_Number ZXBM5210-SP-13; Mouser Part Number 621-ZXBM5210-SP-13
IC3: MP1475DJ-LF-P; TSOT-23-8; Manufacturer_Part_Number MP1475DJ-LF-P
IC5: BU33SD5WG-TR; SOT95P280X125-5N; Manufacturer_Part_Number BU33SD5WG-TR
J9: Motor_L; JST_PH_S6B-PH-K_1x06_P2.00mm_Horizontal
J10: Motor_R; JST_PH_S6B-PH-K_1x06_P2.00mm_Horizontal
J11: BATT; JST_PH_S2B-PH-K_1x02_P2.00mm_Horizontal
L2: 4.7u; L_Wuerth_HCI-5040
R7: 20; R_0402_1005Metric
R8, R9, R17, R18, R19, R20: 100k; R_0402_1005Metric
R10: 16k; R_0402_1005Metric
R11: 40.2k; R_0402_1005Metric
R12: 7.68k; R_0402_1005Metric
R13: 2.7k; R_0402_1005Metric
S3: PWR_SW; Pads_SW

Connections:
+3.3V: C26.1, D3.2 (A), IC5.5 (VOUT), J9.5, J10.5; also elsewhere on the board
+5V: C21.1, C22.1, C24.1, C25.1, IC5.1 (VIN), IC5.3 (STBY), L2.2, R11.1; also elsewhere on the board
+7.5V: C16.1, C18.1, C19.1, C20.1, C27.1, C28.1, IC2.2 (VM), IC2.3 (VDD), IC2.6 (VREF), IC3.2 (IN), IC4.2 (VM), IC4.3 (VDD), IC4.6 (VREF), R8.1, S3.1
/Power&Control/Bat+: J11.1, S3.2
/Power&Control/FB: IC3.8 (FB), R10.2
/Power&Control/OUT_2_L: C33.1, IC2.7 (OUT_2), J9.1
/Power&Control/OUT_2_R: C35.1, IC4.7 (OUT_2), J10.1
/Power&Control/R_Bridge: C24.2, R10.1, R11.2, R12.1
ENC_PA_L: J9.3; also elsewhere on the board
ENC_PA_R: J10.3; also elsewhere on the board
ENC_PB_L: J9.4; also elsewhere on the board
ENC_PB_R: J10.4; also elsewhere on the board
EN/SYNC: IC3.6 (EN/SYNC), R8.2
FWD_L: IC2.4 (FWD), R20.1; also elsewhere on the board
FWD_R: IC4.4 (FWD), R18.1; also elsewhere on the board
GND: C16.2, C18.2, C19.2, C20.2, C21.2, C22.2, C23.2, C25.2, C26.2, C27.2, C28.2, C32.2, C33.2, C34.2, C35.2, IC2.8 (GND), IC2.9 (EP), IC3.4 (GND), IC4.8 (GND), IC4.9 (EP), IC5.2 (GND), J9.2, J10.2, J11.2, R12.2, R13.1, R17.2, R18.2, R19.2, R20.2; also elsewhere on the board
unnamed: C17.1, R7.2
unnamed: D3.1 (K), R13.2
unnamed: IC3.5 (BST), R7.1
unnamed: C23.1, IC3.7 (VCC), R9.2
OUT_1_L: C32.1, IC2.1 (OUT_1), J9.6
OUT_1_R: C34.1, IC4.1 (OUT_1), J10.6
PG: IC3.1 (PG), R9.1
REV_L: IC2.5 (REV), R19.1; also elsewhere on the board
REV_R: IC4.5 (REV), R17.1; also elsewhere on the board
SW: C17.2, IC3.3 (SW), L2.1

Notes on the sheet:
Power
Motors

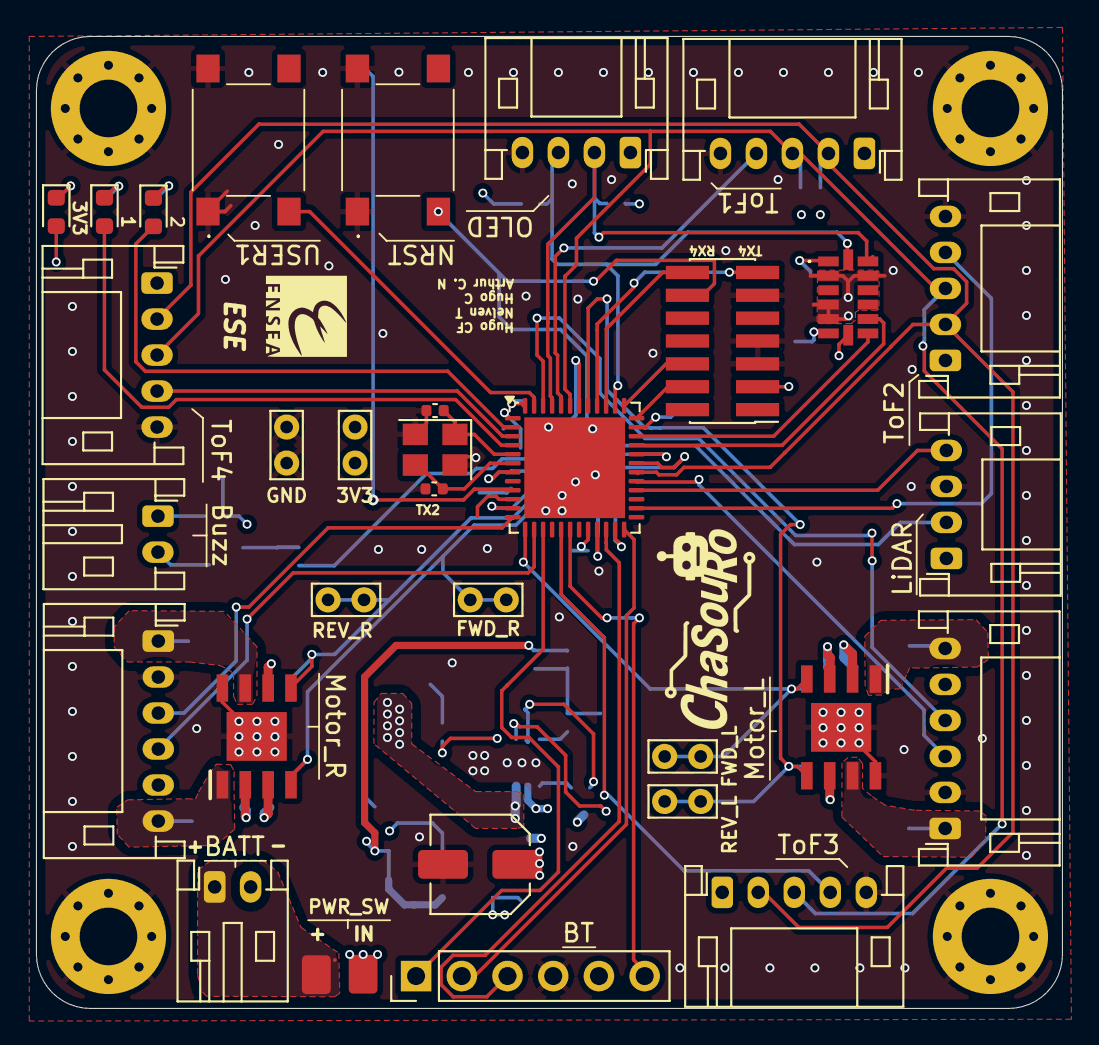
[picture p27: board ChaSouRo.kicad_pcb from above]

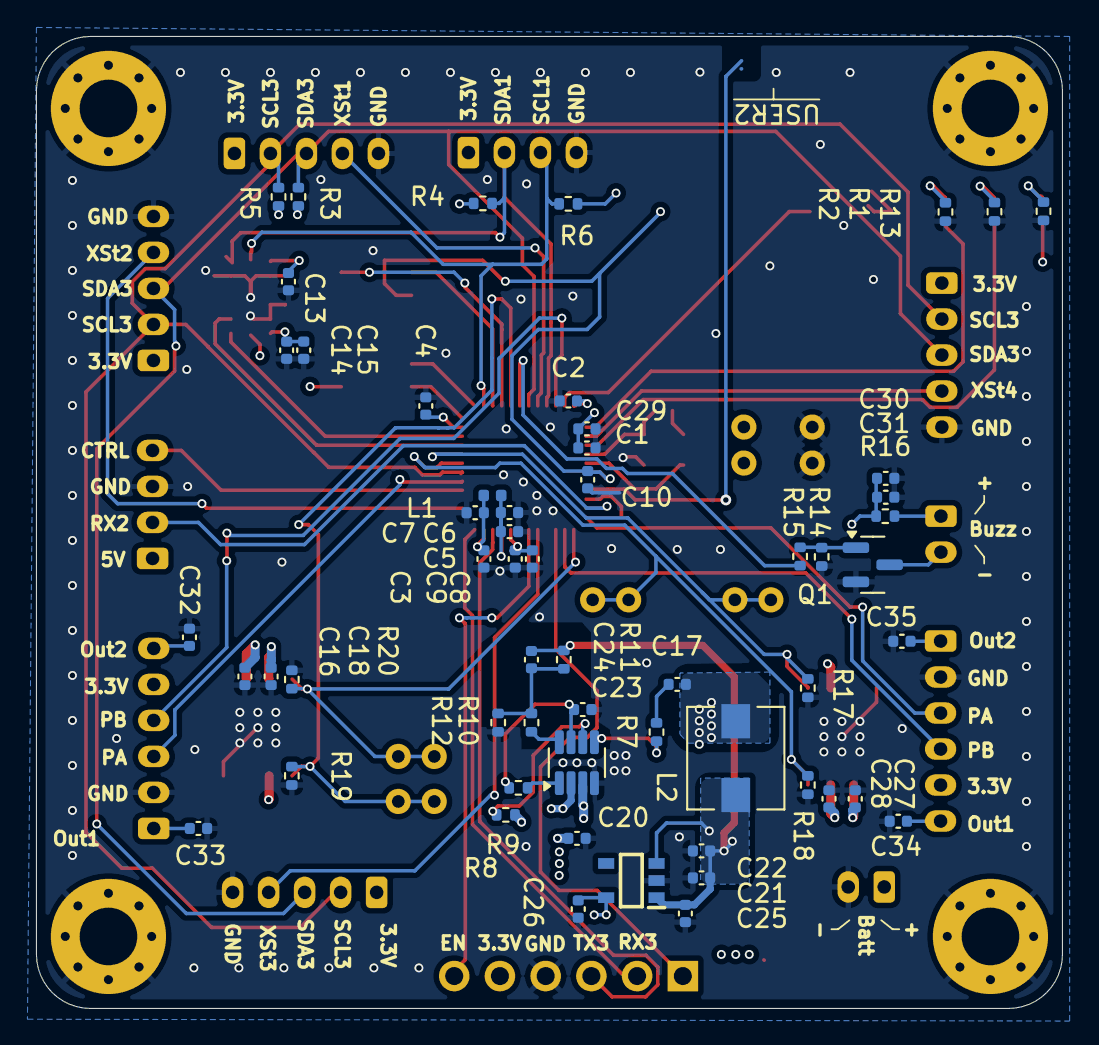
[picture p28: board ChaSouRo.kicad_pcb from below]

Board: 4 copper layers, 57.0 x 54.0 mm, 93 parts (57 on the bottom side), 59 nets.

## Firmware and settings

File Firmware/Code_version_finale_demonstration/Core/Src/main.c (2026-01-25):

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
/* Includes ------------------------------------------------------------------*/
#include "main.h"
#include "cmsis_os.h"
#include "dma.h"
#include "i2c.h"
#include "tim.h"
#include "usart.h"
#include "gpio.h"

/* USER CODE BEGIN Includes */
#include <stdio.h>
#include "actuators/motor.h"
#include "actuators/encoder.h"
// #include "ssd1306.h" Finalement pas utilisee
// #include "ssd1306_fonts.h" Finalement pas utilisee
#include "sensors/accelerometer.h"
#include "actuators/control.h"
#include "actuators/behavior.h"
#include "sensors/tofs.h"
#include "bluetooth/bluetooth.h"
#include "sensors/lidar.h"
//#include "oled.h"
/* USER CODE END Includes */

/* USER CODE BEGIN PTD */
ADXL345_HandleTypeDef hadxl;
/* USER CODE END PTD */


/* USER CODE BEGIN PV */
h_hc05_t h_hc05 =
{
		.huart = &huart3
};
/* USER CODE END PV */

void SystemClock_Config(void);
void MX_FREERTOS_Init(void);
/* USER CODE BEGIN 0 */
//TERMINAL
int __io_putchar(int chr)
{
	HAL_UART_Transmit(&huart4, (uint8_t*) &chr, 1, HAL_MAX_DELAY);
	return chr;
}

//ANTI-REBOND
bool debounce_check(uint32_t *lastTick, TickType_t delay_ms)
{
	TickType_t now = xTaskGetTickCountFromISR();

	if ((now - *lastTick) < pdMS_TO_TICKS(delay_ms))
	{
		return false; // rebond, ignorer
	}
	*lastTick = now;
	return true; // action validée
}

//PROTECTION MEMOIRE
void vApplicationMallocFailedHook(void)
{
	printf("Malloc failed !\r\n"); //n'arrive pas à créé une task (pas de place)
	taskDISABLE_INTERRUPTS();
	for( ;; );
}

//PROTECTION MEMOIRE
void vApplicationStackOverflowHook(TaskHandle_t xTask, char *pcTaskName)
{
	printf("Stack overflow in task %s\r\n", pcTaskName); //Stack overflow
	taskDISABLE_INTERRUPTS();
	for( ;; );
}
/* USER CODE END 0 */

/**
  * @brief  The application entry point.
  * @retval int
  */
int main(void)
{

  /* MCU Configuration--------------------------------------------------------*/

  /* Reset of all peripherals, Initializes the Flash interface and the Systick. */
  HAL_Init();

  /* Configure the system clock */
  SystemClock_Config();

  /* Initialize all configured peripherals */
  MX_GPIO_Init();
  MX_DMA_Init();
  MX_I2C1_Init();
  MX_I2C3_Init();
  MX_TIM2_Init();
  MX_TIM3_Init();
  MX_TIM8_Init();
  MX_UART4_Init();
  MX_USART2_UART_Init();
  MX_USART3_UART_Init();
  MX_TIM16_Init();
  MX_TIM15_Init();
  MX_TIM17_Init();
  /* USER CODE BEGIN 2 */

	/* INITS */
	Init_motors();
	//LIDAR_Init();
	TOFs_Init();
	ENC_Init();
	ADXL345_Init(&hadxl, &hi2c1);
	Control_Init();
	//OLED_Init();

	/* CREATION DES TASKS */
	TOFs_Tasks_Create();
	Control_Tasks_Create();
	Motors_Tasks_Create();
	LIDAR_Tasks_Create();
	ENC_Tasks_Create();
	ADXL345_StartTasks(&hadxl);
	behavior_Tasks_Create();
	HC05_Tasks_Create(&h_hc05);
	//OLED_Tasks_Create();

	/* LANCEMENT DU SCHEDULER */
	vTaskStartScheduler();

  /* USER CODE END 2 */

  /* Call init function for freertos objects (in cmsis_os2.c) */
  MX_FREERTOS_Init();

  /* Start scheduler */
  osKernelStart();

  /* We should never get here as control is now taken by the scheduler */

  /* Infinite loop */
  /* USER CODE BEGIN WHILE */
	while (1)
	{
    /* USER CODE END WHILE */

    /* USER CODE BEGIN 3 */
	}
  /* USER CODE END 3 */
}

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
/* USER CODE BEGIN 4 */
// Finalement pas utilisé
//void HAL_GPIO_EXTI_Callback(uint16_t GPIO_Pin)
//{
//    static TickType_t lastTickUser1 = 0;
//    static uint8_t toggle = 1;
//
//    if (GPIO_Pin == USER1_Pin)
//    {
//        if (!debounce_check(&lastTickUser1, 200))
//            return; // Ignorer rebond
//        if(toggle){
//        	Control_MoveDistanceFromISR(1000);
//			toggle = 0;
//        }
//    }
//}

void HAL_UART_RxHalfCpltCallback(UART_HandleTypeDef *huart)
{
	BaseType_t xHigherPriorityTaskWoken = pdFALSE;

	if (huart == &LID_huartx)
	{
		vTaskNotifyGiveFromISR(htask_LIDAR_Update, &xHigherPriorityTaskWoken);
		portYIELD_FROM_ISR(xHigherPriorityTaskWoken);
	}
}

void HAL_UART_RxCpltCallback(UART_HandleTypeDef *huart)
{
	BaseType_t xHigherPriorityTaskWoken = pdFALSE;

	if (huart == &LID_huartx)
	{
		vTaskNotifyGiveFromISR(htask_LIDAR_Update, &xHigherPriorityTaskWoken);
		portYIELD_FROM_ISR(xHigherPriorityTaskWoken);
	}
	if (huart->Instance==USART3)
	{
		hc05_RX_callback(&h_hc05);
	}
}

/* USER CODE END 4 */

/**
  * @brief  Period elapsed callback in non blocking mode
  * @note   This function is called  when TIM6 interrupt took place, inside
  * HAL_TIM_IRQHandler(). It makes a direct call to HAL_IncTick() to increment
  * a global variable "uwTick" used as application time base.
  * @param  htim : TIM handle
  * @retval None
  */
void HAL_TIM_PeriodElapsedCallback(TIM_HandleTypeDef *htim)
{
  if (htim->Instance == TIM6)
  {
    HAL_IncTick();
  }
  /* USER CODE BEGIN Callback 1 */

	//CODE DES CALLBACKS
	enc_HAL_TIM_PeriodElapsedCallback(htim);
  /* USER CODE END Callback 1 */
}

/**
  * @brief  This function is executed in case of error occurrence.
  * @retval None
  */
void Error_Handler(void)
{
  /* USER CODE BEGIN Error_Handler_Debug */
	/* User can add his own implementation to report the HAL error return state */
	__disable_irq();
	while (1)
	{
		HAL_GPIO_WritePin(GPIOC, LED_D1_Pin, GPIO_PIN_SET);
		HAL_GPIO_WritePin(GPIOC, LED_D2_Pin, GPIO_PIN_SET);
	}
  /* USER CODE END Error_Handler_Debug */
}
#ifdef USE_FULL_ASSERT
/**
  * @brief  Reports the name of the source file and the source line number
  *         where the assert_param error has occurred.
  * @param  file: pointer to the source file name
  * @param  line: assert_param error line source number
  * @retval None
  */
void assert_failed(uint8_t *file, uint32_t line)
{
  /* USER CODE BEGIN 6 */
	/* User can add his own implementation to report the file name and line number,
     ex: printf("Wrong parameters value: file %s on line %d\r\n", file, line) */
  /* USER CODE END 6 */
}
#endif /* USE_FULL_ASSERT */

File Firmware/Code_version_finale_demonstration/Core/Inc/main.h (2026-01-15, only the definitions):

#define LED_D2_Pin GPIO_PIN_13
#define LED_D2_GPIO_Port GPIOC
#define XSHUT4_Pin GPIO_PIN_14
#define XSHUT4_GPIO_Port GPIOC
#define LED_D1_Pin GPIO_PIN_15
#define LED_D1_GPIO_Port GPIOC
#define XSHUT1_Pin GPIO_PIN_1
#define XSHUT1_GPIO_Port GPIOA
#define ENC_PA_R_Pin GPIO_PIN_4
#define ENC_PA_R_GPIO_Port GPIOA
#define FWD_L_Pin GPIO_PIN_5
#define FWD_L_GPIO_Port GPIOA
#define ENC_PB_R_Pin GPIO_PIN_6
#define ENC_PB_R_GPIO_Port GPIOA
#define LED_STATE_Pin GPIO_PIN_7
#define LED_STATE_GPIO_Port GPIOA
#define XSHUT3_Pin GPIO_PIN_0
#define XSHUT3_GPIO_Port GPIOB
#define EN_BT_Pin GPIO_PIN_1
#define EN_BT_GPIO_Port GPIOB
#define XSHUT2_Pin GPIO_PIN_13
#define XSHUT2_GPIO_Port GPIOB
#define ENC_PA_L_Pin GPIO_PIN_6
#define ENC_PA_L_GPIO_Port GPIOC
#define FWD_R_Pin GPIO_PIN_9
#define FWD_R_GPIO_Port GPIOA
#define REV_R_Pin GPIO_PIN_10
#define REV_R_GPIO_Port GPIOA
#define INT_XL2_Pin GPIO_PIN_11
#define INT_XL2_GPIO_Port GPIOA
#define INT_XL1_Pin GPIO_PIN_12
#define INT_XL1_GPIO_Port GPIOA
#define REV_L_Pin GPIO_PIN_3
#define REV_L_GPIO_Port GPIOB
#define Buzzer_Pin GPIO_PIN_4
#define Buzzer_GPIO_Port GPIOB
#define ENC_PB_L_Pin GPIO_PIN_8
#define ENC_PB_L_GPIO_Port GPIOB
#define USER1_Pin GPIO_PIN_9
#define USER1_GPIO_Port GPIOB
#define USER1_EXTI_IRQn EXTI9_5_IRQn

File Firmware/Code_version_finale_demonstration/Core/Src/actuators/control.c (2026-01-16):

/*
 * control.c
 */

#include "actuators/control.h"
#include <math.h>
#include <stdlib.h>

/* ================= GLOBAL ================= */

static ctrl_cmd_t ctrl;
static SemaphoreHandle_t ctrl_mutex;
static QueueHandle_t ctrlQueue;

static PID_t pid_turn;
static PID_t pid_turn_small_angles;
static PID_t pid_move;

/* ================= INIT ================= */

void Control_Init(void)
{
    ctrl_mutex = xSemaphoreCreateMutex();
    configASSERT(ctrl_mutex != NULL);

    ctrlQueue = xQueueCreate(1, sizeof(ctrl_request_t));
    configASSERT(ctrlQueue != NULL);

    ctrl.mode = CTRL_IDLE;

    /* PID rotation */
    PID_Init(&pid_turn,
             KP_TURN, KI_TURN, KD_TURN,
             -MOTOR_PWM_MAX,
              MOTOR_PWM_MAX);

    /* PID rotation */
    PID_Init(&pid_turn_small_angles,
             KP_TURN_SA, KI_TURN_SA, KD_TURN_SA,
             -MOTOR_PWM_MAX,
              MOTOR_PWM_MAX);

    /* PID translation */
    PID_Init(&pid_move,
             KP_MOVE, KI_MOVE, KD_MOVE,
             -MOTOR_PWM_MAX,
              MOTOR_PWM_MAX);
}

void Control_Tasks_Create(void)
{
    if (xTaskCreate(task_Control,
                    "CTRL",
                    128,
                    NULL,
                    task_Control_PRIORITY,
                    NULL) != pdPASS)
    {
        Error_Handler();
    }
}

/* ================= API (TASK) ================= */

void Control_TurnAngle(int32_t angle_deg)
{
    if (xSemaphoreTake(ctrl_mutex, portMAX_DELAY) == pdTRUE)
    {
        ctrl.mode = CTRL_TURN;
        ctrl.target = angle_deg;
        ctrl.start_theta = robot_pose.theta;
        ctrl.target_reached = false;
        xSemaphoreGive(ctrl_mutex);
    }
}

void Control_MoveDistance(int32_t distance_mm)
{
    if (xSemaphoreTake(ctrl_mutex, portMAX_DELAY) == pdTRUE)
    {
        ctrl.mode = CTRL_MOVE;
        ctrl.target = distance_mm;
        ctrl.start_dist = robot_pose.x_dist;
        ctrl.target_reached = false;
        xSemaphoreGive(ctrl_mutex);
    }
}

void Control_Stop(void)
{
    if (xSemaphoreTake(ctrl_mutex, portMAX_DELAY) == pdTRUE)
    {
        ctrl.mode = CTRL_IDLE;
        robot_pose.theta = 0;
        robot_pose.x_dist = 0;
        ctrl.start_theta = 0;
        ctrl.start_dist = 0;
        ctrl.target_reached = true;
        xSemaphoreGive(ctrl_mutex);
    }

    Motors_SetPWM(0, 0);
}

/* ================= API (ISR) ================= */

void Control_TurnAngleFromISR(int32_t angle_deg)
{
    BaseType_t xHigherPriorityTaskWoken = pdFALSE;

    ctrl_request_t req = {
        .mode = CTRL_TURN,
        .target = angle_deg
    };

    xQueueOverwriteFromISR(ctrlQueue, &req, &xHigherPriorityTaskWoken);
    portYIELD_FROM_ISR(xHigherPriorityTaskWoken);
}

void Control_MoveDistanceFromISR(int32_t distance_mm)
{
    BaseType_t xHigherPriorityTaskWoken = pdFALSE;

    ctrl_request_t req = {
        .mode = CTRL_MOVE,
        .target = distance_mm
    };

    xQueueOverwriteFromISR(ctrlQueue, &req, &xHigherPriorityTaskWoken);
    portYIELD_FROM_ISR(xHigherPriorityTaskWoken);
}

void Control_StopFromISR(void)
{
    BaseType_t xHigherPriorityTaskWoken = pdFALSE;

    ctrl_request_t req = {
        .mode = CTRL_IDLE,
        .target = 0
    };

    xQueueOverwriteFromISR(ctrlQueue, &req, &xHigherPriorityTaskWoken);
    portYIELD_FROM_ISR(xHigherPriorityTaskWoken);
}


bool Control_IsBusy(void)
{
    bool busy;

    if (xSemaphoreTake(ctrl_mutex, portMAX_DELAY) == pdTRUE)
    {
        busy = (ctrl.mode != CTRL_IDLE);
        xSemaphoreGive(ctrl_mutex);
    }

    return busy;
}


void Control_WaitUntilNotBusy(void)
{
    if (Control_IsBusy())
    {
        vTaskDelay(pdMS_TO_TICKS(600));
    }
}


/* ================= TASK ================= */

void task_Control(void *arg)
{
    (void)arg;

    TickType_t last = xTaskGetTickCount();

    for (;;)
    {
        /* ===== Réception commandes ISR ===== */
        ctrl_request_t req;
        if (xQueueReceive(ctrlQueue, &req, 0) == pdPASS)
        {
            if (xSemaphoreTake(ctrl_mutex, portMAX_DELAY) == pdTRUE)
            {
                ctrl.mode = req.mode;
                ctrl.target = req.target;

                if (req.mode == CTRL_TURN)
                    ctrl.start_theta = robot_pose.theta;

                if (req.mode == CTRL_MOVE)
                    ctrl.start_dist = robot_pose.x_dist;

                xSemaphoreGive(ctrl_mutex);
            }
        }

        vTaskDelayUntil(&last, pdMS_TO_TICKS(20)); /* 50 Hz */

        ctrl_cmd_t local;
        if (xSemaphoreTake(ctrl_mutex, portMAX_DELAY) == pdTRUE)
        {
            local = ctrl;
            xSemaphoreGive(ctrl_mutex);
        }

        /* ===== IDLE ===== */
        if (local.mode == CTRL_IDLE)
        {
            Motors_SetPWM(0, 0);
            continue;
        }

        /* ===== ROTATION ===== */
        if (local.mode == CTRL_TURN)
        {
            static bool first_call = true;

            if (first_call)
            {
                PID_Reset(&pid_turn);
                first_call = false;
            }

            int32_t target_theta = local.start_theta + local.target;
            int32_t error = target_theta - robot_pose.theta;

            while (error > 180)  error -= 360;
            while (error < -180) error += 360;

            if (abs(error) < ANGLE_THRESHOLD_DEG)
            {
                Control_Stop();
                first_call = true;
                continue;
            }

            int32_t cmd = PID_Compute(&pid_turn, error);
            Motors_SetPWM(cmd, -cmd);
        }



        /* ===== TRANSLATION (POLAIRE) ===== */
        /* ===== TRANSLATION (POLAIRE + MAINTIEN DE CAP) ===== */
        if (local.mode == CTRL_MOVE)
        {
            /* --- Erreur de distance --- */
            int32_t dist = robot_pose.x_dist - local.start_dist;
            int32_t error_dist = local.target - dist;

            /* Arrêt si proche de la cible */
            if (abs(error_dist) < DIST_THRESHOLD_MM)
            {
                PID_Reset(&pid_move);
                PID_Reset(&pid_turn_small_angles);
                Control_Stop();
                continue;
            }

            /* --- Erreur d'angle (heading hold) --- */
            int32_t error_theta = local.start_theta - robot_pose.theta;

            /* Normalisation [-180 ; +180] */
            if (error_theta > 180)  error_theta -= 360;
            if (error_theta < -180) error_theta += 360;

            /* --- PID distance (vitesse moyenne) --- */
            int32_t cmd_dist = PID_Compute(&pid_move, error_dist);

            /* --- Reset intégrale PID angle si vitesse faible (évite windup) --- */
            if (abs(cmd_dist) < 5)
            {
                PID_ResetIntegrator(&pid_turn_small_angles);
            }

            /* --- PID angle (correction différentielle) --- */
            int32_t cmd_theta = PID_Compute(&pid_turn_small_angles, error_theta);
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

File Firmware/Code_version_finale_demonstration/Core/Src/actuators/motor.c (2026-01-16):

/*
 * motor.c
 */

#include "actuators/motor.h"
#include "gpio.h"
#include "FreeRTOS.h"
#include "task.h"

/* ================= GLOBAL ================= */

static volatile int pwm_left_cmd  = 0;
static volatile int pwm_right_cmd = 0;

/* ================= DRIVERS ================= */

MotorDriver motorR = {
    .htim = &htim2,
    .channel_fwd = TIM_CHANNEL_2,
    .channel_rev = TIM_CHANNEL_1
};

MotorDriver motorL = {
    .htim = &htim2,
    .channel_fwd = TIM_CHANNEL_3,
    .channel_rev = TIM_CHANNEL_4
};

/* ================= API ================= */

void Motors_SetPWM(int left, int right)
{
    if (left > MOTOR_PWM_MAX)  left = MOTOR_PWM_MAX;
    if (left < -MOTOR_PWM_MAX) left = -MOTOR_PWM_MAX;

    if (right > MOTOR_PWM_MAX)  right = MOTOR_PWM_MAX;
    if (right < -MOTOR_PWM_MAX) right = -MOTOR_PWM_MAX;

    pwm_left_cmd  = left;
    pwm_right_cmd = right;
}

/* ================= TASK ================= */

void task_motor(void *arg)
{
    (void)arg;
    TickType_t last = xTaskGetTickCount();

    for (;;)
    {
        Motor_SetSpeed(&motorL, pwm_left_cmd);
        Motor_SetSpeed(&motorR, pwm_right_cmd);

        /* 100 Hz */
        vTaskDelayUntil(&last, pdMS_TO_TICKS(10));
    }
}

/* ================= INIT ================= */

void Motors_Tasks_Create(void)
{
    if (xTaskCreate(task_motor,
                    "MOTOR",
                    MOTOR_STACK_SIZE,
                    NULL,
                    task_motor_PRIORITY,
                    NULL) != pdPASS)
    {
        Error_Handler();
    }
}

void Init_motors(void)
{
    HAL_TIM_PWM_Start(motorL.htim, motorL.channel_fwd);
    HAL_TIM_PWM_Start(motorL.htim, motorL.channel_rev);
    HAL_TIM_PWM_Start(motorR.htim, motorR.channel_fwd);
    HAL_TIM_PWM_Start(motorR.htim, motorR.channel_rev);




//    Motor_SetSpeed(&motorL, 300);
//    Motor_SetSpeed(&motorR, -300);
//
//    HAL_Delay(1000);
//
//    Motor_SetSpeed(&motorL, -300);
//    Motor_SetSpeed(&motorR, +300);
//
//    HAL_Delay(1000);
//
//    Motor_SetSpeed(&motorL, 0);
//    Motor_SetSpeed(&motorR, 0);

    Motors_SetPWM(0, 0);



}

/* ================= LOW LEVEL ================= */

void Motor_SetSpeed(MotorDriver *m, int speed)
{
    if (speed > 0) {
        __HAL_TIM_SET_COMPARE(m->htim, m->channel_rev, 0);
        __HAL_TIM_SET_COMPARE(m->htim, m->channel_fwd, speed);
    }
    else if (speed < 0) {
        speed = -speed;
        __HAL_TIM_SET_COMPARE(m->htim, m->channel_fwd, 0);
        __HAL_TIM_SET_COMPARE(m->htim, m->channel_rev, speed);
    }
    else {
        __HAL_TIM_SET_COMPARE(m->htim, m->channel_fwd, 0);
        __HAL_TIM_SET_COMPARE(m->htim, m->channel_rev, 0);
    }
}

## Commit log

2025-09-11 Ajout lib schematic
    [430182070816.stp, ADXL343BCCZ-RL.stp, BU33SD5WG-TR.stp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]
2025-09-12 ajout tof
    [VL53L7 3D Model.step]
2025-09-12 maj 3D
    [UFQFPN-48_7X7X0P55MM.step]
2025-09-26 Ajout PCB
    [ChaSouRo.kicad_pcb, ChaSouRo.kicad_sch, Power&Control.kicad_sch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]
2025-09-28 maj PCB
    [ChaSouRo.kicad_pcb, Power&Control.kicad_sch]
2025-09-28 maj PCB commande
    [ChaSouRo.kicad_pcb, ChaSouRo.kicad_sch, Power&Control.kicad_sch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]
2025-09-29 ajout du code du lidar pas fini
2025-10-01 check pcb LF
    [ChaSouRo.kicad_pcb, ChaSouRo.kicad_sch]
2025-10-01 ajout d'un SW PCB
    [ChaSouRo.kicad_pcb, ChaSouRo.kicad_sch]
2025-10-01 problème d'angles morts corrigé
    [LIDAR.c, LIDAR.h, main.c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]
2025-10-22 Ajout du .ioc
    .ioc à utiliser pour créer le projet cubeIDE avec tous les pins configurés.
2025-10-25 Ajout V2 PCB
    [ChaSouRo.csv, ChaSouRo.kicad_pcb, ChaSouRo.kicad_sch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]
2025-11-12 lidar+enc integre
2025-11-18 odometrie finie, à tester
2025-11-25 commit du code final, LIDAR + encodeurs a optimiser
2025-11-25 commit du code final, LIDAR + encodeurs a optimiser2
2025-11-26 ajout driverMotor code
    + modif du gitignore
2025-11-26 modif pcb
    [ChaSouRo.kicad_pcb]
2025-12-01 modif V2 PCB
    [ChaSouRo.kicad_pcb, ChaSouRo.kicad_sch]
2025-12-02 ajout meca + gcodes
    [ChaSouRo Robot Support.3mf, ChaSouRo Robot Support.gcode.3mf, Robot 3mf.3mf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]
2025-12-02 ajout dma oled
2025-12-03 code LIDAR + enc allégé
2025-12-03 maj oled dma (previous not done)
2025-12-03 modif DriverMotor FreeRTOS non bloquant propre
    [Wheels Robot.3mf, Wheels Robot.gcode.3mf]
2025-12-10 modif drivermotor
2025-12-11 code integre : lidar+enc+moteurs+odom
2025-12-11 code integre : lidar+enc+moteurs+odom+ecran(a finir)
2025-12-26 Update Rapport de projet.md
2026-01-15 maj hardware v2
    [ChaSouRo 2.csv, ChaSouRo 2.kicad_pcb, ChaSouRo 2.kicad_sch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]
2026-01-24 Update Rapport de projet.md
    Tâches réalisées au sein du projet par Arthur
2026-01-25 Update Rapport de projet.md
    Correction images
2026-01-25 Update project report with BOOT0 usage warnings
    Added important note regarding the use of PB4 (BOOT0) and its implications for future projects. Emphasized the risks associated with using BOOT0 on STM32 microcontrollers.

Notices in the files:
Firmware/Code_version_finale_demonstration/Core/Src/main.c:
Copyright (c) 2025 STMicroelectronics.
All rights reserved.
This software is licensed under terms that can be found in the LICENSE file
